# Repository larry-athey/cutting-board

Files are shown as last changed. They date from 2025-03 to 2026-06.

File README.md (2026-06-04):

# Cutting Board
Automated robotic jar advancer for making distillation cuts. Supports pint or quart size Mason jars and requires any 12" - 13" Lazy Susan turntable.

_**This project began on February 19, 2024 and does not yet have a first official release.**_

You may contact me directly at https://panhandleponics.com<br>
Subscribe to the official YouTube channel at https://www.youtube.com/@PanhandlePonics<br>

**Facebook Idiot:** _Why would you bother?_<br>
**Me:** It's only a "bother" for somebody who couldn't do it on their best day. I'd rather have nicer things.

---
<br>
---

This project is the result of numerous requests for the same additional feature to the [RPi Smart Still](https://github.com/larry-athey/rpi-smart-still) system. However, this would actually be a stand-alone device rather than a feature of that system.

_Keep in mind that this is a prototype project, not a cosmetically polished product that I intend to sell as a kit. These aren't hard to build, but if you're not a computer/electronics hobbyist, you'll want to find somebody who is to build one for you. Honestly, kids in STEM classes build this kind of stuff all the time._

Many people seem to think that it's possible for a computer to know what flavors they prefer _(or not)_ in their distillate. Sorry, AI can't even do that because it would require gas chromatography to determine what's in there at what concentrations, and that's anything but a quick process. Then the AI would need to be trained on what you like or dislike. Seriously, lay off the sci-fi movies, they're anything but based on reality.

No, Genio and iStill don't have this capability, either. The most they can do is pause the run so you can toss your heads/foreshots based on the volume and ABV of the wash in your boiler. What's more, it's just based on an approximation using simple math, there's honestly nothing high tech about what they're doing.

This device allows you to automate your cuts by automatically swapping out jars once they are filled about 1/2 inch from the top. These can be pint or quart size Mason jars placed on the 3D printed turntable segments attached to any 12" - 13" Lazy Susan turntable under your condenser or parrot outlet. The calibration procedure is simple and only needs to be performed one time.

---

_Oddly enough, even after posting numerous YouTube videos on this project, some people still think this is supposed to be something more than a robotic jar advancer with a jar-full switch. One more time for the people asleep in the back of the room, **you can't do electronic cuts by flavor compound without slowpoke gas chromatography!** Even if you did, by the time you get your results, they would say that you needed to switch jars a couple hours ago._

---

## Theory of Operation

The system design is based on two 20mm Nema 17 stepper motors, an optical switch, and a capacitve touch switch connected to a LilyGo T-Display S3 touch screen ESP32 module. One motor drives the turntable using gear drive by way of a TPU 3D printed geared pulley against the geared edge of a custom 3D printed turntable top. The other motor drives a custom linear actuator that raises and lowers an arm with a capacitive touch switch to detect when a jar is full.

Once a jar is full, the liquid will come into contact with a copper dipstick/antenna at the end of the arm to trigger a capacitive touch switch. This tells the ESP32 to raise the arm, advance the turntable 45 degrees to the next jar position, then lower the arm again. There is an optical switch is on the linear actuator frame itself to detect when it is at it's zero position. A calibration procedure runs at every startup to find the zero position of the linear actuator.

An optional feed arm may be attached that uses a 1/4" ID silicone tube from the proofing parrot to the jar that automatically kinks the tube between jar switches. Not a requirement and not really necessary if you are using wide-mouth jars. But, the travel time between small-mouth jars can lead to a bit of mess on the turntable without it.

_**NOTE:** If you are making absolute lighter fluid (the typical Still Spirits T500 fare) the capacitive touch switch may not detect when a jar is full until it's right up to the brim. This is because the density of pure ethanol is so incredibly low. Weigh a pint of water and a pint of 90% ethanol and you'll see what I mean. There's no flavor to that crap anyway, so you might as well just fill gallon jugs and not waste your time with cuts._

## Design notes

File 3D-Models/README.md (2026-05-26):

# 3D Model Notes

No, I haven't put any effort into a fancy case here because this whole project is nothing but a prototype, it's pretty much just a 3D printed version of what Radio Shack used to sell. The front half of the [Airhead](https://github.com/larry-athey/airhead) case and buttons are used for the LilyGo T-Display S3 here. Install your Lilygo in the front half of the case and use four M3 bolts and nuts to mount it to the **CB-Case-Top.stl** model.

Ultimately, my plan is to have the case for the LilyGo T-Display S3 and all of the electronics joined together with the motor mount and linear actuator. This plan kinda got put on the back burner because of other tasks, so this is a slow work in progress.

<br>

The model **CB-Flange-Gripper.stl** should be printed with TPU or other rubber-like filament to reduce noise and vibrations. A 22 mm flange from Amazon (https://www.amazon.com/dp/B0BF46M4NH) was used to attach it to the stepper motor. I recommend attaching the gripper to the flange with silicone and allowing it to set up, then use 10 mm M2 self-tapping screws to lock it in place. This allows you to make sure that the gripper is centered on the flange before driving screws into it.

Since the linear actuator that raises and lowers the float arm is nothing high tech, it will be noisy at times unless you add some kind of buffer on the internal slider. For example, I applied blue painter's tape to the sides and back of **CB-Riser-Inside-Pint.stl** to tame down vibration noise. Most arts & crafts stores sell velvet tape to prevent items from scratching table tops, which would probably be a better choice in this case.

The model **CB-Turntable-Segment.stl** must be printed four times and needs to be attached to the top of a 12" to 13" Lazy Susan to form a full circle. These provide placement markers for your jars and the gear drive that the model **CB-Flange-Gripper.stl** meshes with. You will want to apply some sort of [non-skid surface](https://www.amazon.com/dp/B0DZXWTQV2) or silicone coasters to the placement markers to keep your jars in place and immune to vibrations. Make absolutely sure that these four segments are perfectly centered and there are no gaps between them.

If you are running a larger still and need to fill quart jars, you will want to use the **CB-Riser-Inside-Quart.stl** model instead of the pint size version that I used. The vertical travel distance is still the same, you're just using a taller inside riser with the linear actuator.

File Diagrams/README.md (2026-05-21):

# Cutting Board Electronics

You may notice that the printed circuit board used here isn't as fancy as the boards for my other projects. The reason being, I created it with the Fritzing program which is geared for hobbyists. If somebody else wants to create a fancier board, I'll happily accept it and replace the current one. PCB design just isn't my forte, EasyEDA and KiCad annoy me to no end.

Keep in mind that the LilyGo T-Display S3 mounts to the bottom side of the PCB and only uses the pins on the bottom edge of the board _(note the +3V and +5V identifiers for orientation)_. This is intentional to make the motor and sensor connections serviceable without the need to disasseble the whole controller unit.

The footprint for VR1 looks like a TO-220 mounting for an LM7803, but is intended for a small 3.3 volt buck regulator which are available from various sources that use the same footprint. I don't recommend using an LM7803 due to the heat that they all generate.

Fritzing didn't allow me to label the pins of the screw terminals for the sensors. If you're looking at the screw terminals straight on with the top of the PCB upward, the GND is on the left, the +3V is on the right, and the signal line is in the middle.

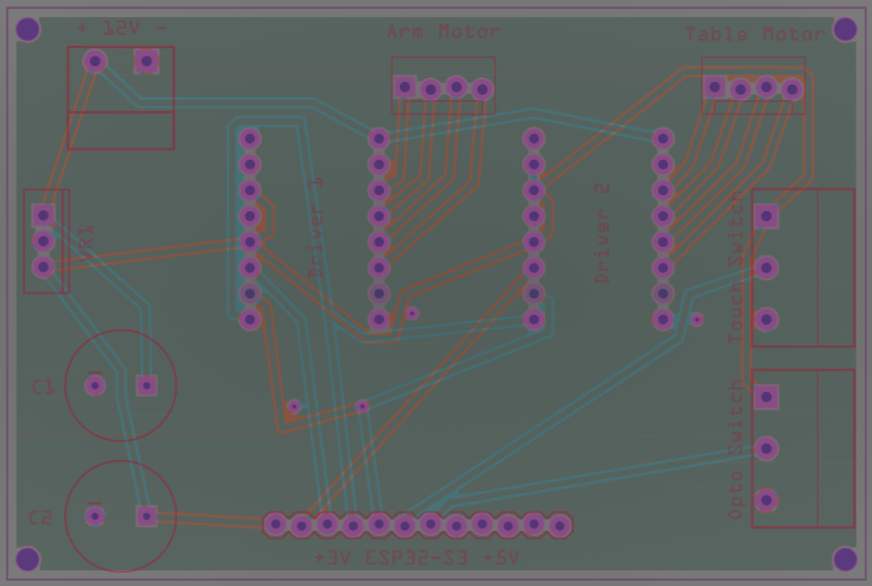
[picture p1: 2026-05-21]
Diagrams/Cutting-Board-PCB_layers.png

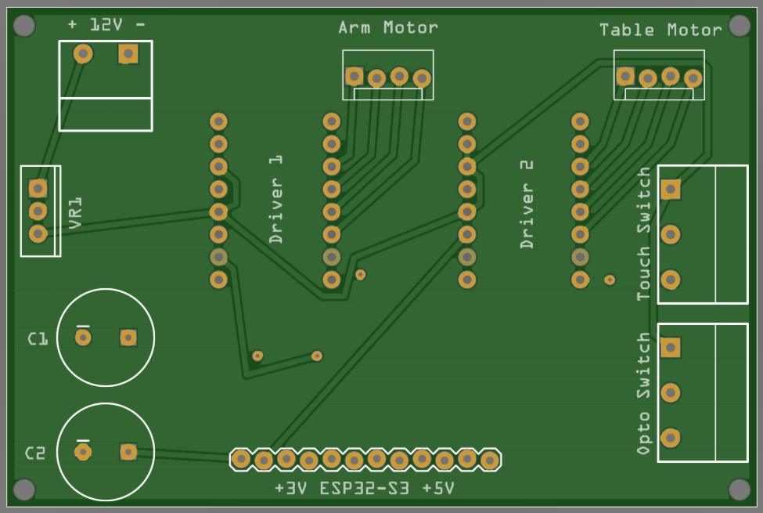
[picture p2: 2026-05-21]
Diagrams/Cutting-Board-PCB_top.png

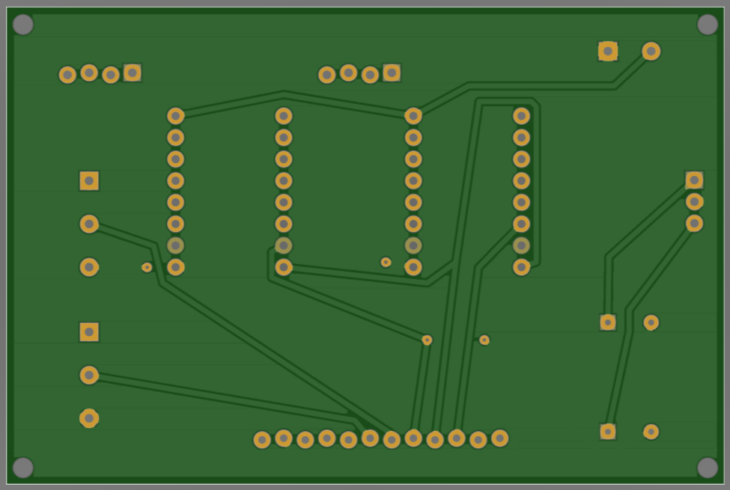
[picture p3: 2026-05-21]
Diagrams/Cutting-Board-PCB_bottom.png

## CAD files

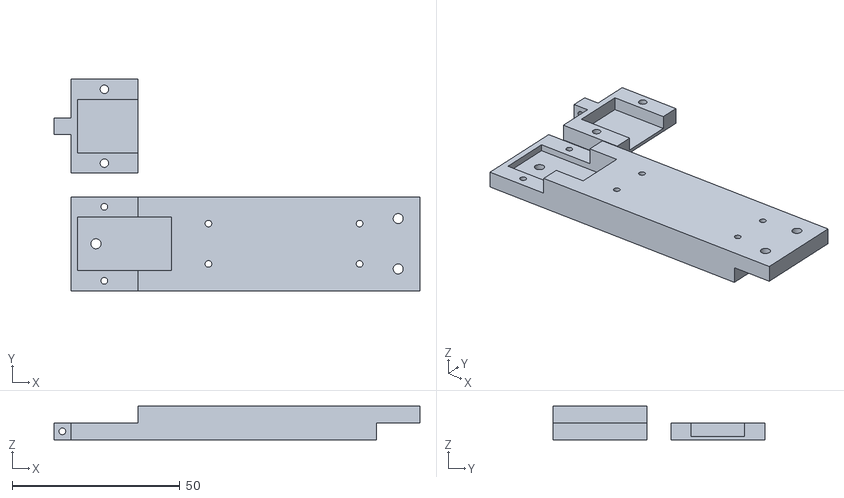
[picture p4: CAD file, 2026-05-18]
3D-Models/CB-Detector-Arm.stl
109.0 x 63.0 x 10.0

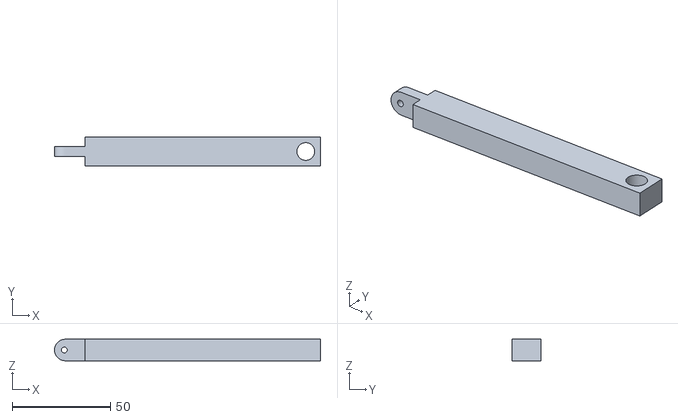
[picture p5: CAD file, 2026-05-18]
3D-Models/CB-Feed-Arm.stl
135.5 x 15.0 x 11.0

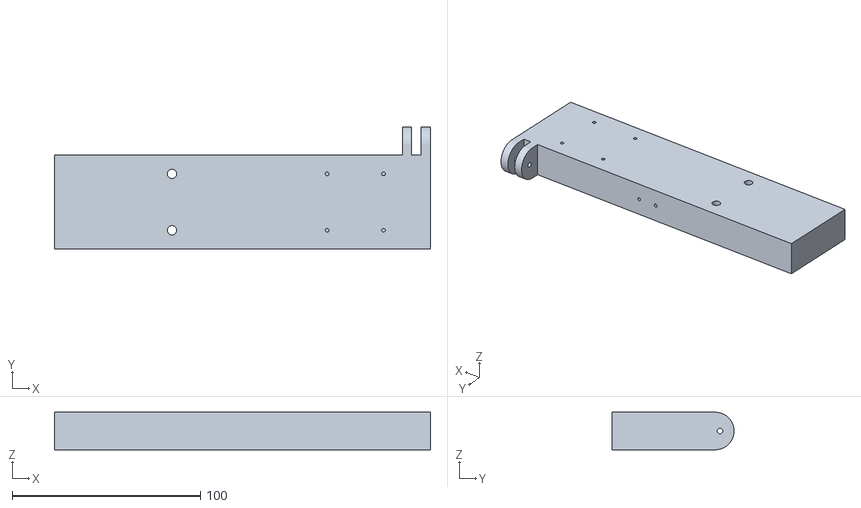
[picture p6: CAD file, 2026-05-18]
3D-Models/CB-Motor-Mount.stl
200.0 x 65.0 x 20.0

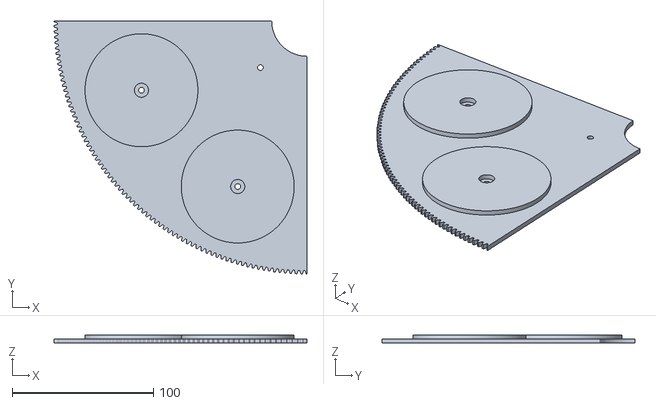
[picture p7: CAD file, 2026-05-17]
3D-Models/CB-Turntable-Segment.stl
179.3 x 179.3 x 6.00

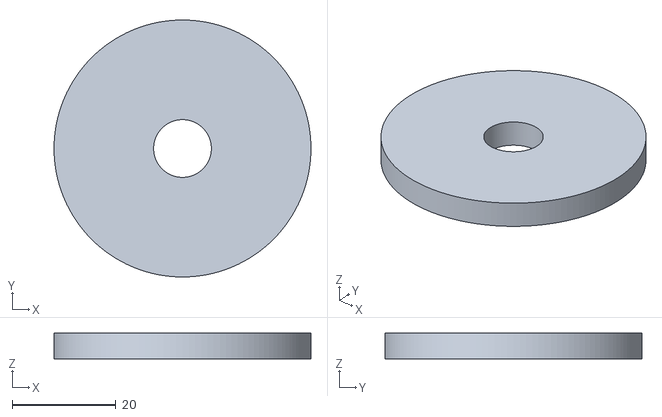
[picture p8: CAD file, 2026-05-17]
3D-Models/CB-Turntable-Centering-Guide.stl
49.5 x 49.5 x 5.00

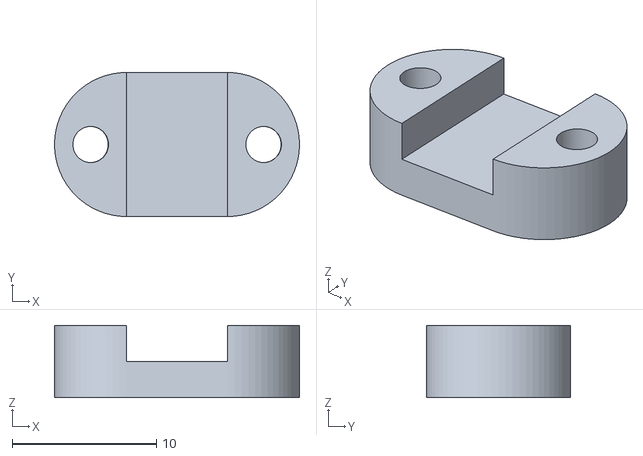
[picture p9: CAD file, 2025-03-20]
3D-Models/CB-Arm-Ribbon-Clamp.stl
17.0 x 10.0 x 5.00

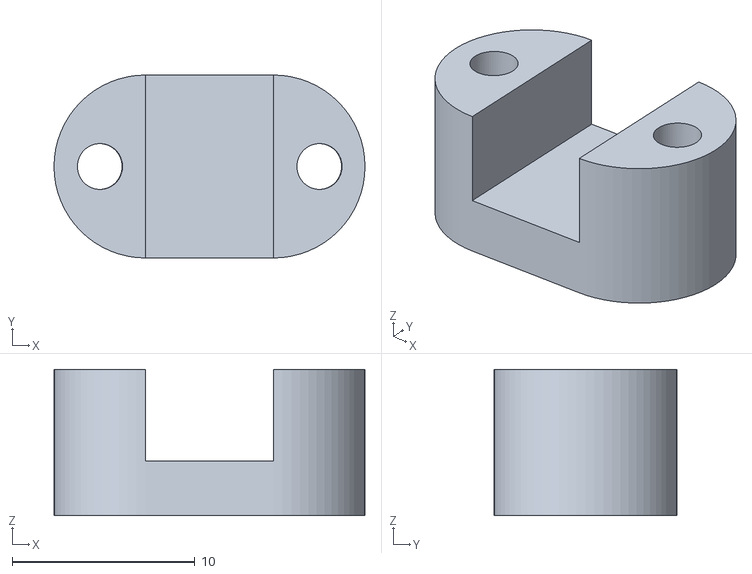
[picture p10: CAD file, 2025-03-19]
3D-Models/CB-Ribbon-Clamp.stl
17.0 x 10.0 x 8.00

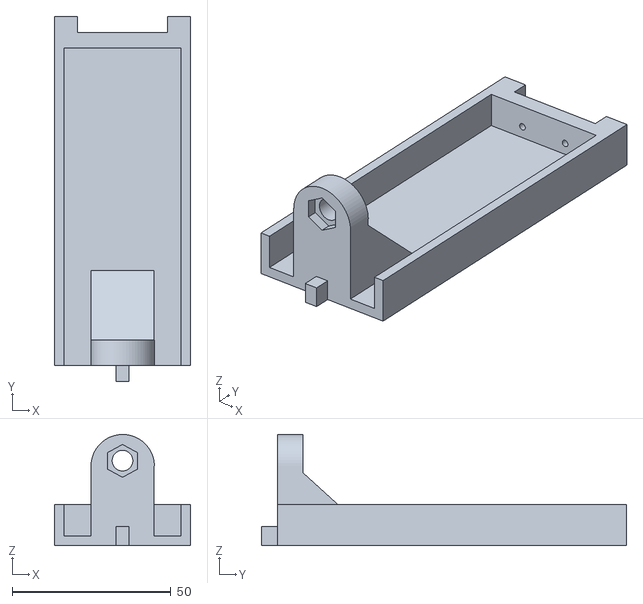
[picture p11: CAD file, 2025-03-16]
3D-Models/CB-Riser-Inside-Quart.stl
43.0 x 115.0 x 35.0

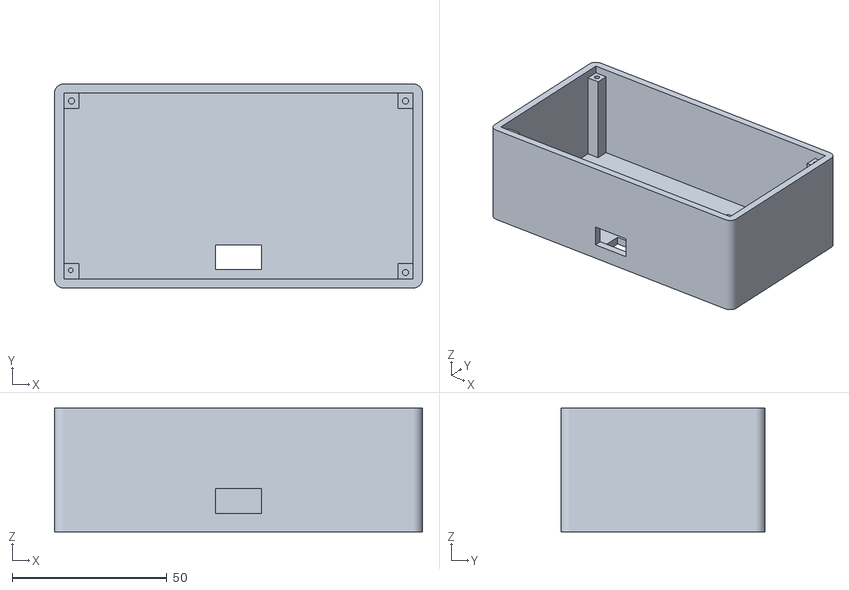
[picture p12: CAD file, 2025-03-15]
3D-Models/CB-Case-Bottom.stl
119.0 x 66.0 x 40.0

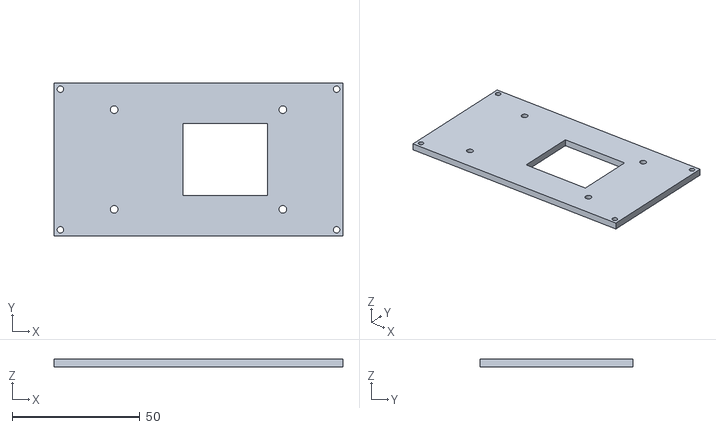
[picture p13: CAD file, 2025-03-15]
3D-Models/CB-Case-Top.stl
113.0 x 60.0 x 3.00

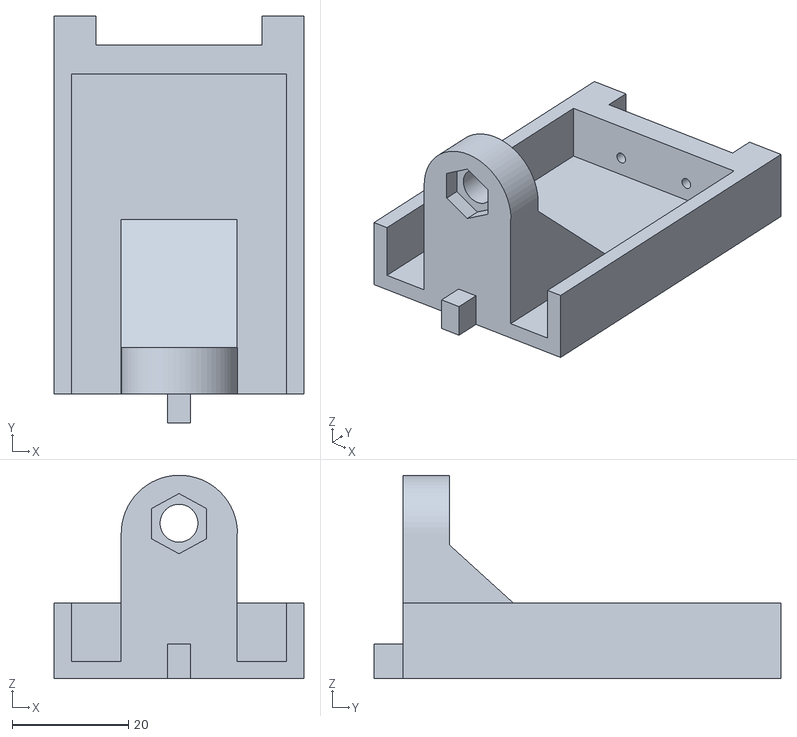
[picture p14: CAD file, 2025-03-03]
3D-Models/CB-Riser-Inside-Pint.stl
43.0 x 70.0 x 35.0

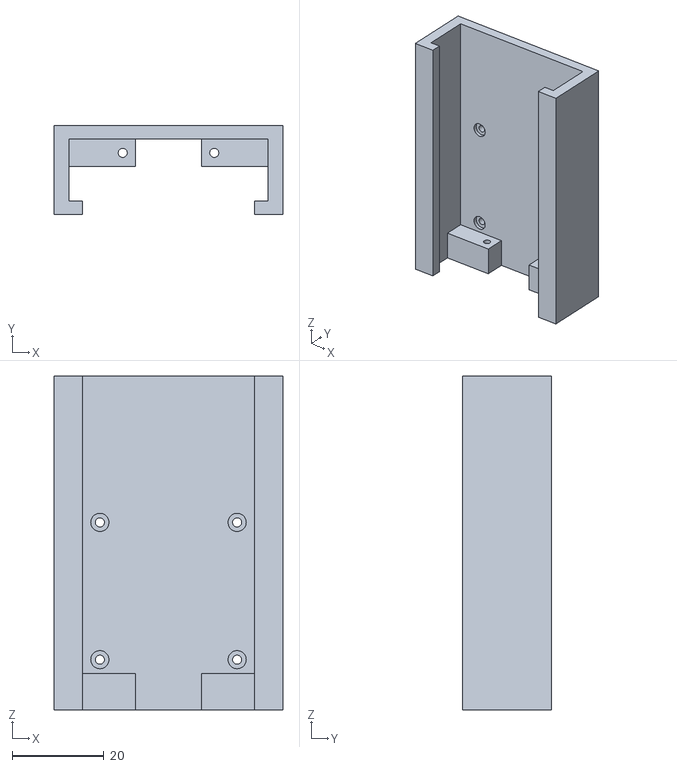
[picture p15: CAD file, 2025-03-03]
3D-Models/CB-Riser-Outside.stl
50.0 x 19.5 x 73.0

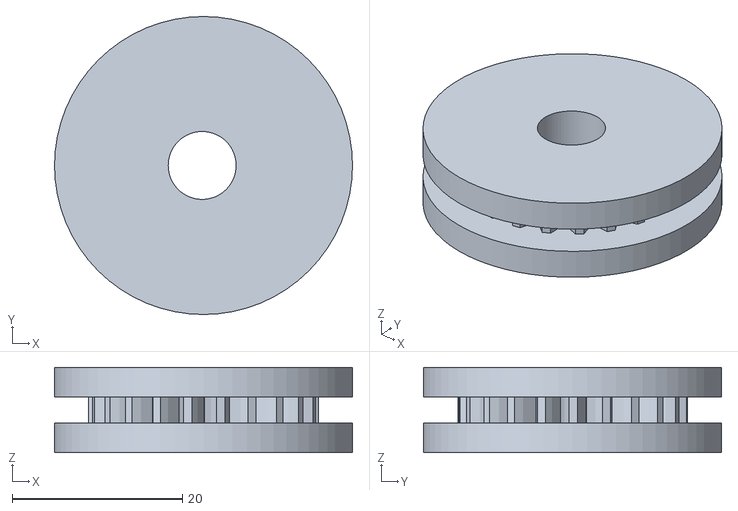
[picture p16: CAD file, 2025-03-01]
3D-Models/CB-Flange-Gripper.stl
35.0 x 35.0 x 10.0

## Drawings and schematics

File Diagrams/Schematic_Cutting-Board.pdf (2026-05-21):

## LilyGo T-Display S3 Touch

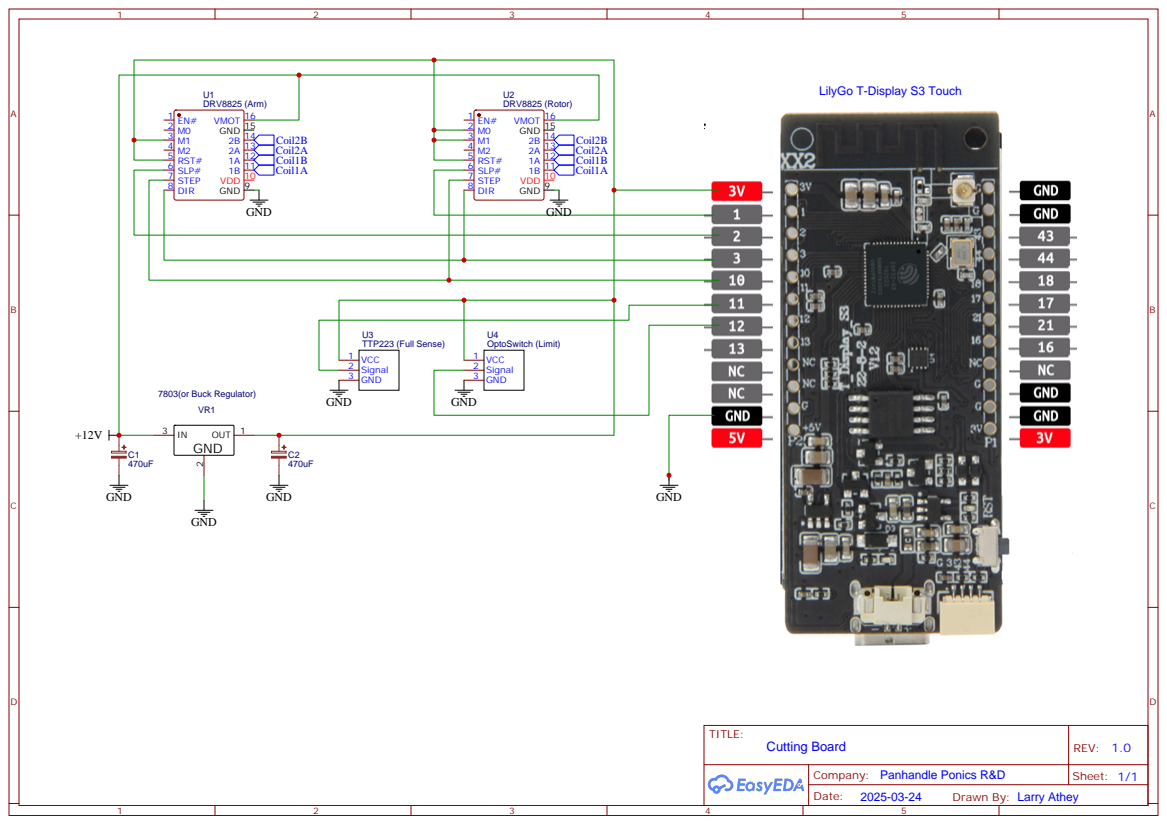
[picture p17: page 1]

Drawn By: Larry Athey

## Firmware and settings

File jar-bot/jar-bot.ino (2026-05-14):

//------------------------------------------------------------------------------------------------
// Jar-Bot - Cutting Board Brain | (CopyLeft) 2025-Present | Larry Athey (https://panhandleponics.com)
//
// Tested up to Espressif ESP32 v2.0.14 due to LilyGo requirements
//
// This code requires the LilyGo T-Display-S3 ESP32 board. You will first need to properly set up
// your Arduino IDE to upload to that board. See: https://github.com/Xinyuan-LilyGO/T-Display-S3
// Make sure that you only install the Espressif ESP32 v2.0.14 board library since the 3.x stuff
// is not backward compatible and will throw syntax errors all over the place. (Nice fkin upgrade)
//
// The TTP223 capacitive touch switch uses a 4" dipstick soldered to the touch plate area of the
// PCB. This is made from a piece of 14 gauge solid core wire from common household Romex cable.
// Cut off a piece about 4.5" long, strip 1/2" from one end and 1/4" from the other. Bend a loop
// in the 1/2" end and solder it to the touch plate. Add a 33pf capacitor between the touch plate
// and ground because this dipstick will become a big antenna and will pick up tons of RF noise.
// 
// NOTE: The DRV8825 for the float arm is configured for 1/4 steps and 1/8 steps for the rotor.
//       Refer to the M0/M1/M2 connections in the schematic. Adjust the Vref for each DRV8825
//       driver to 0.32V while the motors are running.
//------------------------------------------------------------------------------------------------
#include "Arduino_GFX_Library.h" // Standard GFX library for Arduino, built with version 1.4.9
#include "FreeSans9pt7b.h"       // https://github.com/moononournation/ArduinoFreeFontFile.git 
#include "Preferences.h"         // ESP32 Flash memory read/write library
#include "Wire.h"                // I2C communications library for touch-screen interface
#define TOUCH_MODULES_CST_SELF   // Tell TouchLib.h to use the CST816 chip routines
#include "TouchLib.h"            // LilyGo touch-screen interface library
//------------------------------------------------------------------------------------------------
// Internal GPIO constants
#define SCL 17                   // I2C clock pin
#define SDA 18                   // I2C data pin
#define SCREEN_BACKLIGHT 38      // Screen backlight LED pin
#define SCREEN_POWER_ON 15       // Screen power on/off pin
#define INC_BTN 0                // Value + button
#define DEC_BTN 14               // Value - button
#define TOUCH_INT 16             // CPU interrupt monitor pin for touch-screen input hook
#define TOUCH_RES 21             // Reset pin for touch-screen controller chip
// External GPIO constants
#define STEPPER_ENABLE_1 1       // Rotor stepper motor driver enable
#define STEPPER_ENABLE_2 2       // Arm stepper motor driver enable
#define STEPPER_DIRECTION 3      // Stepper motor direction (paralleled for both DRV8825 drivers)
#define STEPPER_PULSE 10         // Stepper motor pulse line (paralleled for both DRV8825 drivers)
#define TOUCH_SWITCH 11          // TTP223 touch switch signal pin (formerly an optical switch)
#define ARM_ZERO_SWITCH 12       // Optical arm zero position sense pin
//------------------------------------------------------------------------------------------------
bool GotInterrupt = false;       // True if touch input has been detected on the screen
long LoopCounter = 0;            // Used for debouncing the touch screen
int RotorSize = 20736;           // Rotor (turntable) circumference in motor steps
int JarDistance = RotorSize / 8; // Total motor steps between jars (motor steps to move 45 degrees)
int ArmUpperPos = 32000;         // Float arm upper position (800 steps per mm of vertical lift)
int ArmLowerPos = 16000;         // Float arm lower position "                                 "
int ArmCurrentPos = 0;           // Current vertical position of the float arm
int ArmPulse = 200;              // Float Arm stepper pulse width per on/off state (microseconds)
int RotorPulse = 800;            // Rotor stepper pulse width per on/off state (microseconds)
int RotorSteps = 1600;           // Rotor stepper motor steps per revolution
int ArmSteps = 800;              // Float arm stepper motor steps per revolution
byte CurrentMode = 1;            // 1 = Home Screen, 2 = Rotor Config, 3 = Float Arm Config
byte ActiveButton = 1;           // Currently selected touch-screen button
String Version = "1.0.1";        // Current release version of the project
//------------------------------------------------------------------------------------------------
// Home screen button coordinates (CurrentMode = 1)
int PrevJarX1 = 0, PrevJarY1 = 0, PrevJarX2 = 158, PrevJarY2 = 84;
int NextJarX1 = 160, NextJarY1 = 0, NextJarX2 = 319, NextJarY2 = 84;
int RotConfX1 = 0, RotConfY1 = 86, RotConfX2 = 158, RotConfY2 = 169;
int ArmConfX1 = 160, ArmConfY1 = 86, ArmConfX2 = 319, ArmConfY2 = 169;
// Configuration button coordinates (CurrentMode = 2/3)
int Conf1_X1 = 0, Conf1_Y1 = 86, Conf1_X2 = 105, Conf1_Y2 = 169;
int Conf2_X1 = 107, Conf2_Y1 = 86, Conf2_X2 = 213, Conf2_Y2 = 169;
int Conf3_X1 = 215, Conf3_Y1 = 86, Conf3_X2 = 319, Conf3_Y2 = 169;
// RGB values for the button and text colors
#define JARBTN RGB565(0,215,0)
#define MODEBTN RGB565(50,50,230)
#define CONFBTN RGB565(0,210,210)
#define TESTBTN RGB565(0,215,0)
#define HILITE RGB565(230,230,230)
#define BTNTEXT RGB565(245,245,245)
//------------------------------------------------------------------------------------------------
Arduino_DataBus *bus = new Arduino_ESP32PAR8Q(7 /* DC */, 6 /* CS */, 8 /* WR */, 9 /* RD */,39 /* D0 */, 40 /* D1 */, 41 /* D2 */, 42 /* D3 */, 45 /* D4 */, 46 /* D5 */, 47 /* D6 */, 48 /* D7 */);
Arduino_GFX *gfx = new Arduino_ST7789(bus, 5 /* RST */, 0 /* rotation */, true /* IPS */, 170 /* width */, 320 /* height */, 35 /* col offset 1 */, 0 /* row offset 1 */, 35 /* col offset 2 */, 0 /* row offset 2 */);
Arduino_Canvas_Indexed *canvas = new Arduino_Canvas_Indexed(320 /* width */, 170 /* height */, gfx);
TouchLib Touch(Wire,SDA,SCL,CTS820_SLAVE_ADDRESS,TOUCH_RES);
//------------------------------------------------------------------------------------------------
Preferences preferences;
//------------------------------------------------------------------------------------------------
void setup() {
  // Enable serial communications for debugging output
  Serial.begin(9600);
  delay(1000);
  Serial.println("");

  // Initialize the external device GPIO pins
  pinMode(STEPPER_ENABLE_1,OUTPUT); digitalWrite(STEPPER_ENABLE_1,LOW);
  pinMode(STEPPER_ENABLE_2,OUTPUT); digitalWrite(STEPPER_ENABLE_2,LOW);
  pinMode(STEPPER_PULSE,OUTPUT);
  pinMode(STEPPER_DIRECTION,OUTPUT);
  pinMode(TOUCH_SWITCH,INPUT_PULLDOWN);  // GPIO pin goes high when the switch is activated
  pinMode(ARM_ZERO_SWITCH,INPUT_PULLUP); // GPIO pin goes low when the light beam is obstructed

  // Get the last calibration settings from flash memory
  GetMemory();
  if (JarDistance == 0) {
    // New chip, flash memory not initialized
    if (Serial) Serial.println("Initializing flash memory");
    RotorSize   = 20736;
    ArmUpperPos = 32000;
    ArmLowerPos = 16000;
    SetMemory();
  }

  // Initialize the touch-screen reset line
  pinMode(TOUCH_RES,OUTPUT);
  digitalWrite(TOUCH_RES,LOW);
  delay(500);
  digitalWrite(TOUCH_RES,HIGH);

  Wire.begin(SDA,SCL);
  if (Touch.init()) {
    pinMode(TOUCH_INT,INPUT_PULLUP);
    attachInterrupt(TOUCH_INT,[] { GotInterrupt = true; },FALLING);
    if (Serial) Serial.println("Touch screen interface initialized");
  } else {
    if (Serial) Serial.println("Touch screen interface not detected");
  }

  // Power up the screen and backlight
  pinMode(SCREEN_POWER_ON,OUTPUT);
  digitalWrite(SCREEN_POWER_ON,HIGH);
  ledcSetup(0,2000,8);
  ledcAttachPin(SCREEN_BACKLIGHT,0);
  ledcWrite(0,255); // Screen brightness (0-255)
  pinMode(INC_BTN,INPUT_PULLUP);
  pinMode(DEC_BTN,INPUT_PULLUP);

  // Initialize the graphics library and blank the screen
  gfx->begin();
  gfx->setRotation(3);
  gfx->fillScreen(BLACK);

  // In order to eliminate screen flicker, everything is plotted to an off-screen buffer and popped onto the screen when done
  canvas->begin();
  ScreenUpdate();

  // Initialize the float arm by raising it 5 mm and then lowering it until the lower limit switch triggers
  PopoverMessage("Calibrating Float Arm");
  InitializeArm();
  // Move the float arm to its down position
  SetArmPos(ArmLowerPos);
  ScreenUpdate();

  LoopCounter = millis();
}
//------------------------------------------------------------------------------------------------
void GetMemory() { // Get the last calibration settings from flash memory on startup
  preferences.begin("prefs",true);
  RotorSize   = preferences.getUInt("rotor_size",0);
  ArmUpperPos = preferences.getUInt("arm_upper_pos",0);
  ArmLowerPos = preferences.getUInt("arm_lower_pos",0);
  preferences.end();
  JarDistance = RotorSize / 8;
}
//------------------------------------------------------------------------------------------------
void SetMemory() { // Update flash memory with the current calibration settings
  preferences.begin("prefs",false);
  preferences.putUInt("rotor_size",RotorSize);
  preferences.putUInt("arm_upper_pos",ArmUpperPos);
  preferences.putUInt("arm_lower_pos",ArmLowerPos);
  preferences.end();
  JarDistance = RotorSize / 8;
}
//------------------------------------------------------------------------------------------------
void InitializeArm() { // Set the float arm to it's lower limit position to locate absolute zero
  digitalWrite(STEPPER_ENABLE_2,HIGH);
  delay(10);
  digitalWrite(STEPPER_DIRECTION,LOW);
  for (int x = 1; x <= (ArmSteps * 5); x ++) { // Raise the arm 5 mm (threaded rod with 1 mm pitch)
    digitalWrite(STEPPER_PULSE,HIGH);
    delayMicroseconds(ArmPulse);
    digitalWrite(STEPPER_PULSE,LOW);
    delayMicroseconds(ArmPulse);
  }
  digitalWrite(STEPPER_DIRECTION,HIGH);
  while(digitalRead(ARM_ZERO_SWITCH) == HIGH) { // Lower the arm to find zero
    digitalWrite(STEPPER_PULSE,HIGH);
    delayMicroseconds(ArmPulse);
    digitalWrite(STEPPER_PULSE,LOW);
    delayMicroseconds(ArmPulse);
  }
  digitalWrite(STEPPER_ENABLE_2,LOW);
}
//------------------------------------------------------------------------------------------------
void SetArmPos(int Position) { // Move the float arm up or down to a specific position
  int Steps;
  bool Limit = false;
  long Uptime = millis();

  if (Position > ArmCurrentPos) {
    digitalWrite(STEPPER_DIRECTION,LOW);
    Steps = Position - ArmCurrentPos;
  } else if (Position < ArmCurrentPos) {
    digitalWrite(STEPPER_DIRECTION,HIGH);
    Steps = ArmCurrentPos - Position;
  } else {
    return;
  }
  digitalWrite(STEPPER_ENABLE_2,HIGH);
  delay(10);
  for (int x = 1; x <= Steps; x ++) {
    digitalWrite(STEPPER_PULSE,HIGH);
    delayMicroseconds(ArmPulse);
    digitalWrite(STEPPER_PULSE,LOW);
    delayMicroseconds(ArmPulse);
    if ((Uptime > 15000) && (digitalRead(ARM_ZERO_SWITCH) == LOW)) {
      ArmCurrentPos = 0;
      Limit = true;
      break;
    }
  }
  digitalWrite(STEPPER_ENABLE_2,LOW);
  if (! Limit) ArmCurrentPos = Position;
}
//------------------------------------------------------------------------------------------------
void BumpArm(byte Direction, int Steps, bool Hold) {
  if ((Direction == 0) && (digitalRead(ARM_ZERO_SWITCH) == LOW)) {
    ArmCurrentPos = 0;
    return;
  }
  if (Direction == 1) {
    digitalWrite(STEPPER_DIRECTION,LOW);
  } else {
    digitalWrite(STEPPER_DIRECTION,HIGH);
  }
  if (! Hold) {
    digitalWrite(STEPPER_ENABLE_2,HIGH);
    delay(10);
  }
  for (int x = 1; x <= Steps; x ++) {
    digitalWrite(STEPPER_PULSE,HIGH);
    delayMicroseconds(ArmPulse);
    digitalWrite(STEPPER_PULSE,LOW);
    delayMicroseconds(ArmPulse);
    if (digitalRead(ARM_ZERO_SWITCH) == LOW) {
      ArmCurrentPos = 0;
      break;
    } else {
      if (Direction == 1) {
        ArmCurrentPos ++;
      } else {
        ArmCurrentPos --;
      }
    }
  }
  if (! Hold) digitalWrite(STEPPER_ENABLE_2,LOW);
}
//------------------------------------------------------------------------------------------------
void SwitchJars(byte Direction) { // Rotates the turntable/rotor 45 degrees forward or backward
  digitalWrite(STEPPER_DIRECTION,Direction);
  digitalWrite(STEPPER_ENABLE_1,HIGH);
  delay(10);
  for (int x = 1; x <= JarDistance; x ++) {
    digitalWrite(STEPPER_PULSE,HIGH);
    delayMicroseconds(RotorPulse);
    digitalWrite(STEPPER_PULSE,LOW);
    delayMicroseconds(RotorPulse);
  }
  digitalWrite(STEPPER_ENABLE_1,LOW);
}
//-----------------------------------------------------------------------------------------------
void JarAdvance(byte Direction) { // Lift the arm, switch jars, lower the arm
  ScreenUpdate();
  if (Serial) {
    if (Direction == 1) {
      Serial.println("Mode 1 Jar Advance +");
    } else {
      Serial.println("Mode 1 Jar Advance -");
    }
  }
  PopoverMessage("New Jar Selected");
  if (Serial) Serial.println("Raising Float Arm");
  SetArmPos(ArmUpperPos);
  if (Serial) Serial.println("Advancing Jar Position");
  SwitchJars(Direction);
  if (Serial) Serial.println("Lowering Float Arm");
  SetArmPos(ArmLowerPos);
}
//-----------------------------------------------------------------------------------------------
void BumpRotor(byte Direction, int Steps, bool Hold) {
  digitalWrite(STEPPER_DIRECTION,Direction);
  if (! Hold) {
    digitalWrite(STEPPER_ENABLE_1,HIGH);
    delay(10);
  }
  for (int x = 1; x <= Steps; x ++) {
    digitalWrite(STEPPER_PULSE,HIGH);
    delayMicroseconds(RotorPulse);
    digitalWrite(STEPPER_PULSE,LOW);
    delayMicroseconds(RotorPulse);
  }
  if (! Hold) digitalWrite(STEPPER_ENABLE_1,LOW);
}
//------------------------------------------------------------------------------------------------
void DrawButton(byte WhichOne) { // Draws and highlights the specified button on the screen
  canvas->setFont(&FreeSans9pt7b);
  canvas->setTextColor(BTNTEXT);
  if (WhichOne == 0) {
    canvas->fillRoundRect(PrevJarX1,PrevJarY1,PrevJarX2 - PrevJarX1,PrevJarY2 - PrevJarY1,5,JARBTN);
    canvas->setCursor(PrevJarX1 + 28,PrevJarY1 + 45);
    canvas->print("Previous Jar");
    if (ActiveButton == 0) canvas->drawRoundRect(PrevJarX1,PrevJarY1,PrevJarX2 - PrevJarX1,PrevJarY2 - PrevJarY1,5,HILITE);
  } else if (WhichOne == 1) {
    canvas->fillRoundRect(NextJarX1,NextJarY1,NextJarX2 - NextJarX1,NextJarY2 - NextJarY1,5,JARBTN);
    canvas->setCursor(NextJarX1 + 45,NextJarY1 + 45);
    canvas->print("Next Jar");
    if (ActiveButton == 1) canvas->drawRoundRect(NextJarX1,NextJarY1,NextJarX2 - NextJarX1,NextJarY2 - NextJarY1,5,HILITE);
  } else if (WhichOne == 2) {
    canvas->fillRoundRect(RotConfX1,RotConfY1,RotConfX2 - RotConfX1,RotConfY2 - RotConfY1,5,MODEBTN);
    canvas->setCursor(RotConfX1 + 40,RotConfY1 + 33);
    canvas->print("Configure");
    canvas->setCursor(RotConfX1 + 41,RotConfY1 + 57);
    canvas->print("Turntable");
    if (ActiveButton == 2) canvas->drawRoundRect(RotConfX1,RotConfY1,RotConfX2 - RotConfX1,RotConfY2 - RotConfY1,5,HILITE);
  } else if (WhichOne == 3) {
    canvas->fillRoundRect(ArmConfX1,ArmConfY1,ArmConfX2 - ArmConfX1,ArmConfY2 - ArmConfY1,5,MODEBTN);
    canvas->setCursor(ArmConfX1 + 41,ArmConfY1 + 33);
    canvas->print("Configure");
    canvas->setCursor(ArmConfX1 + 33,ArmConfY1 + 57);
    canvas->print("Sensor Arm");
    if (ActiveButton == 3) canvas->drawRoundRect(ArmConfX1,ArmConfY1,ArmConfX2 - ArmConfX1,ArmConfY2 - RotConfY1,5,HILITE);
  } else if (WhichOne == 4) {
    canvas->fillRoundRect(Conf1_X1,Conf1_Y1,Conf1_X2 - Conf1_X1,Conf1_Y2 - Conf1_Y1,5,CONFBTN);
    canvas->setCursor(Conf1_X1 + 34,Conf1_Y1 + 33);
    canvas->print("Zero");
    canvas->setCursor(Conf1_X1 + 31,Conf1_Y1 + 57);
    canvas->print("Rotor");
    if (ActiveButton == 4) canvas->drawRoundRect(Conf1_X1,Conf1_Y1,Conf1_X2 - Conf1_X1,Conf1_Y2 - Conf1_Y1,5,HILITE);
  } else if (WhichOne == 5) {
    canvas->fillRoundRect(Conf2_X1,Conf2_Y1,Conf2_X2 - Conf2_X1,Conf2_Y2 - Conf2_Y1,5,CONFBTN);
    canvas->setCursor(Conf2_X1 + 17,Conf2_Y1 + 33);
    canvas->print("Measure");
    canvas->setCursor(Conf2_X1 + 31,Conf2_Y1 + 57);
    canvas->print("Rotor");
    if (ActiveButton == 5) canvas->drawRoundRect(Conf2_X1,Conf2_Y1,Conf2_X2 - Conf2_X1,Conf2_Y2 - Conf2_Y1,5,HILITE);
  } else if (WhichOne == 6) {
    canvas->fillRoundRect(Conf3_X1,Conf3_Y1,Conf3_X2 - Conf3_X1,Conf3_Y2 - Conf3_Y1,5,TESTBTN);
    canvas->setCursor(Conf3_X1 + 32,Conf3_Y1 + 33);
    canvas->print("Test");
    canvas->setCursor(Conf3_X1 + 19,Conf3_Y1 + 57);
    canvas->print("Settings");
    if (ActiveButton == 6) canvas->drawRoundRect(Conf3_X1,Conf3_Y1,Conf3_X2 - Conf3_X1,Conf3_Y2 - Conf3_Y1,5,HILITE);
  } else if (WhichOne == 7) {
    canvas->fillRoundRect(Conf1_X1,Conf1_Y1,Conf1_X2 - Conf1_X1,Conf1_Y2 - Conf1_Y1,5,CONFBTN);
    canvas->setCursor(Conf1_X1 + 40,Conf1_Y1 + 33);
    canvas->print("Set");
    canvas->setCursor(Conf1_X1 + 31,Conf1_Y1 + 57);
    canvas->print("Lower");
    if (ActiveButton == 7) canvas->drawRoundRect(Conf1_X1,Conf1_Y1,Conf1_X2 - Conf1_X1,Conf1_Y2 - Conf1_Y1,5,HILITE);
  } else if (WhichOne == 8) {
    canvas->fillRoundRect(Conf2_X1,Conf2_Y1,Conf2_X2 - Conf2_X1,Conf2_Y2 - Conf2_Y1,5,CONFBTN);
    canvas->setCursor(Conf2_X1 + 40,Conf2_Y1 + 33);
    canvas->print("Set");
    canvas->setCursor(Conf2_X1 + 31,Conf2_Y1 + 57);
    canvas->print("Upper");
    if (ActiveButton == 8) canvas->drawRoundRect(Conf2_X1,Conf2_Y1,Conf2_X2 - Conf2_X1,Conf2_Y2 - Conf2_Y1,5,HILITE);
  } else if (WhichOne == 9) {
    canvas->fillRoundRect(Conf3_X1,Conf3_Y1,Conf3_X2 - Conf3_X1,Conf3_Y2 - Conf3_Y1,5,TESTBTN);
    canvas->setCursor(Conf3_X1 + 32,Conf3_Y1 + 33);
    canvas->print("Test");
    canvas->setCursor(Conf3_X1 + 19,Conf3_Y1 + 57);
    canvas->print("Settings");
    if (ActiveButton == 9) canvas->drawRoundRect(Conf3_X1,Conf3_Y1,Conf3_X2 - Conf3_X1,Conf3_Y2 - Conf3_Y1,5,HILITE);
  }
}
//------------------------------------------------------------------------------------------------
void PopoverMessage(String Msg) { // Display popover message to the user
  int16_t nX = 0, nY = 0, TextX;
  uint16_t nWidth = 0, nHeight = 0;

  canvas->setFont(&FreeSans9pt7b);
  canvas->setTextColor(BLACK);
  canvas->getTextBounds(Msg,0,0,&nX,&nY,&nWidth,&nHeight);
  TextX = round(nWidth / 2);
  canvas->fillRoundRect(160 - TextX - 12,60,nWidth + 26,40,5,WHITE);
  canvas->drawRoundRect(160 - TextX - 12,60,nWidth + 26,40,5,BLACK);
  canvas->setCursor(160 - TextX,85);
  canvas->print(Msg);
  canvas->flush();
}
//------------------------------------------------------------------------------------------------
void ScreenUpdate() { // Plot the off-screen buffer and then pop it to the touch screen display
  if (CurrentMode == 1) {
    if (Serial) {
      // Debugging information
      Serial.println();
      Serial.print("RotorSize: "); Serial.println(RotorSize);
      Serial.print("JarDistance: "); Serial.println(JarDistance);
      Serial.print("ArmUpperPos: "); Serial.println(ArmUpperPos);
      Serial.print("ArmLowerPos: "); Serial.println(ArmLowerPos);
      Serial.print("ArmCurrentPos: "); Serial.println(ArmCurrentPos);
      Serial.println();
    }

    canvas->fillScreen(BLACK);
    DrawButton(0);
    DrawButton(1);
    DrawButton(2);
    DrawButton(3);
  } else {
    canvas->fillScreen(DARKGREY);
    canvas->setFont(&FreeSans9pt7b);
    canvas->setTextColor(BTNTEXT);
    if (CurrentMode == 2) {
      canvas->setCursor(10,20);
      canvas->print("Zero Rotor: use +/- to set start point");
      canvas->setCursor(10,45);
      canvas->print("Measure: rotate turntable + 360 deg");
      canvas->setCursor(10,70);
      canvas->print("Test: verify 45 degree jar divisions");
      DrawButton(4);
      DrawButton(5);
      DrawButton(6);
    } else {
      canvas->setCursor(10,20);
      canvas->print("Set Lower: use +/- to set arm down");
      canvas->setCursor(10,45);
      canvas->print("Set Upper: use +/- to set arm raised");
      canvas->setCursor(10,70);
      canvas->print("Test: verify the arm up/down points");
      DrawButton(7);
      DrawButton(8);
      DrawButton(9);
    }
  }
  canvas->flush();
}
//-----------------------------------------------------------------------------------------------
bool RegionPressed(int Xpos,int Ypos,int X1,int Y1,int X2,int Y2) { // Screen button press evaluator
  if ((Xpos >= X1) && (Xpos <= X2) && (Ypos >= Y1) && (Ypos <= Y2)) {
    return true;
  } else {
    return false;
  }
}
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
void loop() {

}
*/
//------------------------------------------------------------------------------------------------

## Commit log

2025-02-20 Create Flange Gripper.stl
    [Flange Gripper.stl]
2025-02-20 Update Flange Gripper.stl
    [Flange Gripper.stl]
2025-03-01 Renamed the flange gripper model
    [CB-Flange-Gripper.stl]
2025-03-02 Riser model updates
    [CB-Riser-Inside-Pint.stl, CB-Riser-Outside.stl]
2025-03-02 Model updates to increase opto switch mounting hole size
    [CB-Float-Arm.stl, CB-Riser-Inside-Pint.stl, CB-Riser-Outside.stl]
2025-03-03 Add float actuator models
    [CB-Float-Actuator.stl, CB-Riser-Inside-Pint.stl, CB-Riser-Outside.stl]
2025-03-15 Create case models
    [CB-Case-Bottom.stl, CB-Case-Top.stl]
2025-03-15 update rotor bump values and case models
    [CB-Case-Bottom.stl, CB-Case-Top.stl]
2025-03-19 Model updates
    [CB-Motor-Mount.stl, CB-Ribbon-Clamp.stl]
2025-03-20 Rename arm cable clamp model
    [CB-Arm-Clamp.stl, CB-Arm-Ribbon-Clamp.stl]
2025-03-20 Float arm model updates
    [CB-Float-Actuator.stl, CB-Float-Arm.stl]
2026-05-13 3D model updates
    [CB-Detector-Arm.stl, CB-Float-Actuator.stl, CB-Float-Arm.stl]
2026-05-21 Add PCB diagram
2026-05-21 Add PCB images
2026-05-21 PCB updates
